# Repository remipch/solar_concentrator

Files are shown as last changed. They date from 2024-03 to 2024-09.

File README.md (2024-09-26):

# Solar Concentrator :sunny:

This project is a homemade automated solar concentrator :wrench: :sunny: :mag_right:

- [Overview](#overview)
- [Caution](#caution)
- [Key points](#key-points)
- [Technical breakdown](#technical-breakdown)
- [Next step](#next-step)
- [Licenses](#licenses)

## Overview

It consists of:
* An orientable mirror panel (currently 48 focusing mirrors, totaling 1m²)
* A fixed target (currently a simple concrete oven with a black metal plate and a tempered glass)
* The supervisor: an electronic control device that measures the target, computes and sends commands to the motors

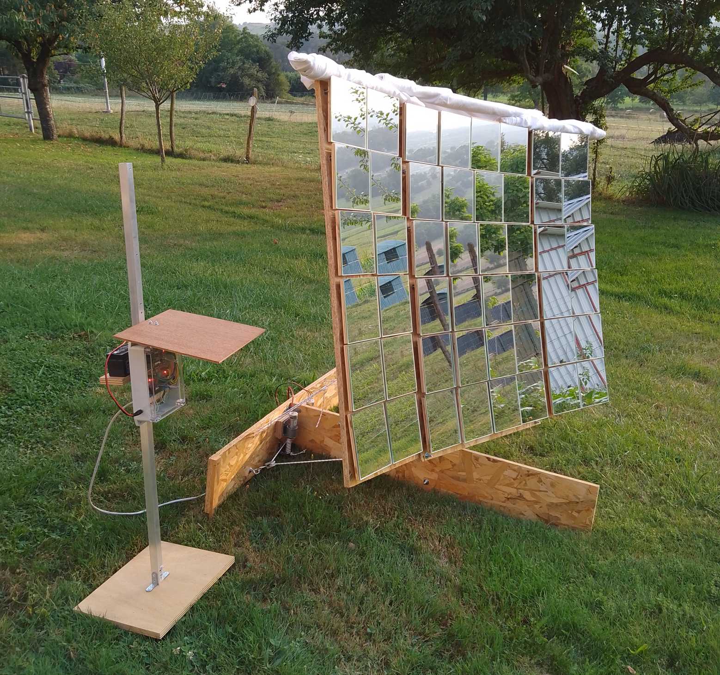
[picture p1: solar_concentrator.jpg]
Solar Concentrator


On 26 june 2024, when adding some aluminium foil inside the oven to improve insulation,
the oven temperature has risen to __210°C after 30 minutes__.

The video below shows the concentrator in action on 8 July 2024:
* First half of the video is the assembly (speed x10)
* Second half is the automatic sun tracking for about 7 hours (speed x600)

https://github.com/user-attachments/assets/06e3a9e1-d853-4ddd-b5d8-55cf9d6ecc89

## Caution

> [!CAUTION]
> :warning::warning: __THIS PROJECT MAY HARM PEOPLE OR ANIMALS IN THE SURROUNDINGS__ :warning::warning:
>
> It can __cause permanent blindness, burn skin or ignite objects__.
>
> Even when the concentrator is not powered, the sun remains concentrated 48 times in a single small area.
>
> This focal point is constantly __moving along a path that is difficult to predict__.
>
> In its current state, it __must be continuously monitored__ and the mirrors must be covered quickly in the event of an anomaly.

## Key points

* Can produce up to about __1000 watts of heat__ while __consuming 3.8 watts__ of electrical power :moneybag:
* Uses only standard, cheap and available components and materials :bricks: :nut_and_bolt:
* Does not require a high precision construction, everything can be built by hand with common tools :straight_ruler: :carpentry_saw:
* Easy to assemble and disassemble :screwdriver:
* Easy to understand and modify :mag_right:
* Open source :unlock:

Limitations of this version:
* There is no safety layer implemented (see warning above :warning:)
* An initial manual step is required to orient the panel before it can automatically track the sun
* Only one panel can be controlled
* Does not work on cloudy days (it is the user's responsibility to remove the clouds from the sky :smile:)
* Power consumption could be significantly reduced through the implementation of various low-power modes

To build this project, some products were happily "hacked" out of their original use:
* The tempered glass used in the oven is from an [Ikea shelf](https://www.ikea.com/fr/fr/p/komplement-tablette-en-verre-blanc-80257647/)
* The mirrors are [decorative bathroom mirrors](https://www.bricoman.fr/lot-6-miroirs-adhesif-carre-15x15-cm-1429043.html)
* The motors are cheap [model engines](https://www.gotronic.fr/art-motoreducteur-mfa-950d8101ln-11376.htm)

## Technical breakdown

The project structure reflects the technical breakdown.

Detailed information can be found in the corresponding subfolders:

* [Mechanics :gear:](mechanics/README.md) : 3D models of the parts used in the solar panel
* [Electronics :electric_plug:](electronics/README.md) : schematics and layout of the custom supervisor board
* Software :floppy_disk: :
    * [Simulator](software/simulator/README.md) : evaluates the theoretical power received by the target for a given hardware configuration
    * Supervisor controller : ESP32-CAM firmware based on [Espressif ESP32 framework](https://docs.espressif.com/projects/esp-idf/en/latest/esp32/index.html)
        * [Supervisor component](software/supervisor_controller/components/supervisor/README.md) defines the supervisor high level logic
        * [Sun tracker](software/supervisor_controller/components/sun_tracker/README.md) computes motors commands to keep the sun light at the center of the target area
        * [Target detector](software/supervisor_controller/components/target_detector/README.md) detects the target position in image
        * [Web interface](software/supervisor_controller/components/web_interface/README.md) allows the user to interact with the supervisor
        * [Motors component](software/supervisor_controller/components/motors/README.md) controls the motors from the ESP32 application
        * [Image component](software/supervisor_controller/components/image/README.md) provides general image processing functions
    * [Motors controller](software/motors_controller/README.md) : Arduino Pro Mini firmware for controlling motors

## Next step

The next step is to control any number of panels to obtain a power output of several kilowatts.

This would open up the following possibilities:
* Quickly boil a large volume of liquid
* Desalinate or sterilize a large volume of water
* Cook or sterilize a large volume of food
* Melt plastic, metal or glass
* Increase the output of photovoltaic panels with [concentrated photovoltaics](https://en.wikipedia.org/wiki/Concentrator_photovoltaics)

## Licenses

Copyright (C) 2024 Rémi Peuchot (https://remipch.github.io/)

* The software is distributed under [GNU GPL v3](LICENSE.md)
* Hardware designs (electronics and mechanics) are distributed under [CERN Open Hardware Licence v2 Strongly Reciprocal](LICENSE-HW.txt)

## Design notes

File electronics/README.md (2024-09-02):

# Solar Concentrator Electronics :electric_plug:

This folder contains the custom electronics designed for the supervisor.

- [Overview](#overview)
- [Supervisor Board](#supervisor-board)
    - [Schematics](#schematics)
    - [Components](#components)
    - [Top layer](#top-layer)
    - [Bottom layer](#bottom-layer)
    - [3D model](#3d-model)
    - [Photos](#photos)
    - [BOM](#bom)
- [Electronic case](#electronic-case)
    - [Photos](#photos)
    - [BOM](#bom)

## Overview

A custom board has been designed using [LibrePCB](https://librepcb.org) and produced by [AISLER](https://aisler.net).

It doesn't do anything complicated, just glues things together :
* Allows to connect the ESP32-CAM board
* Allows to connect the Arduino Pro Mini board
* Includes connectors for 2 mirror panels
* Includes a voltage regulator to convert the battery voltage from 12V to 5V
* Includes some switches to turn ON/OFF the child boards
* Includes a FTDI connector to upload the ESP32-CAM firmware in place (Arduino has its own FTDI connector)
* Includes a minimal voltage converter for the child boards to communicate with each other

Everything is assembled in an electronic case with a few external connectors for power and panels.

> [!NOTE]
> The electronics can control two panels but the current software only controls one.

Electronics overview

## Supervisor Board

### Schematics

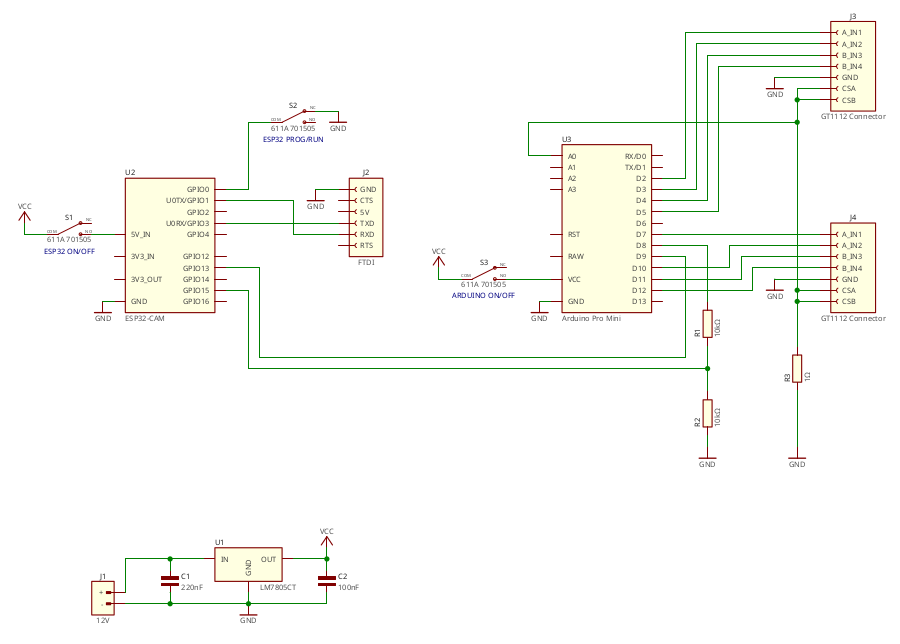
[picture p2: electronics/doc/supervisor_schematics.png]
Supervisor board schematics


### Components

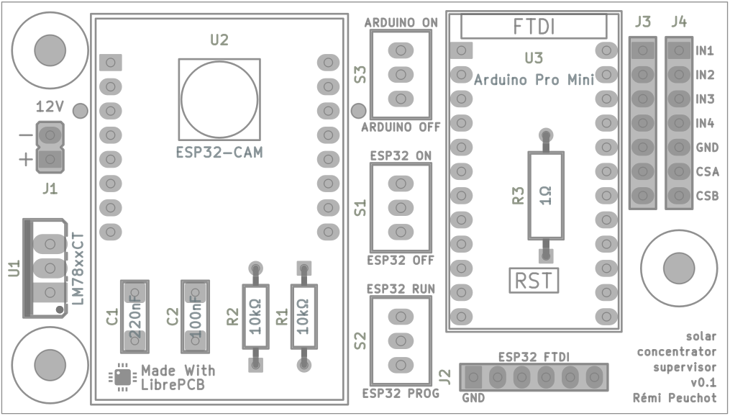
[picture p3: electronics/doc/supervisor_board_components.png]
Supervisor board components


### Top layer

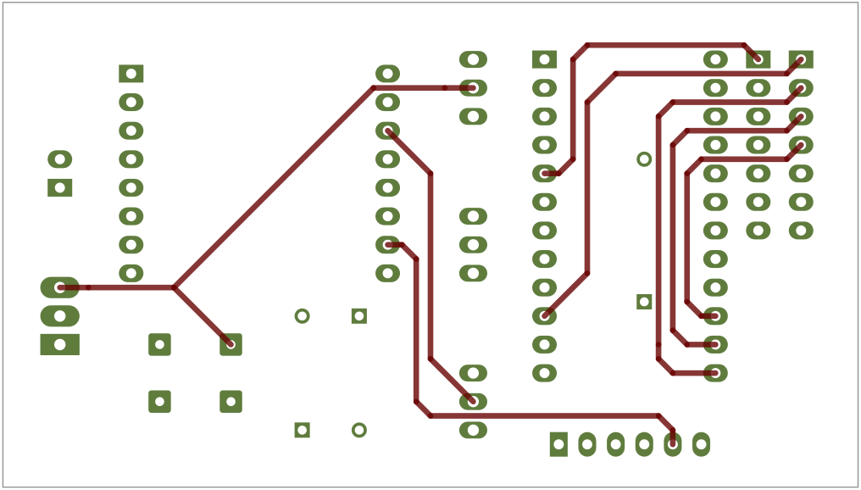
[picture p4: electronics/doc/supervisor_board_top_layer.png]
Supervisor board top layer


(ground plane is not shown)

### Bottom layer

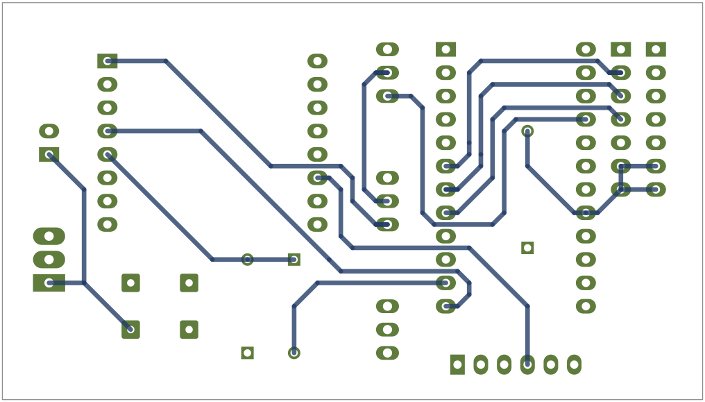
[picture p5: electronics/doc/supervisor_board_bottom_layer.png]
Supervisor board bottom layer


(ground plane is not shown)

### 3D model

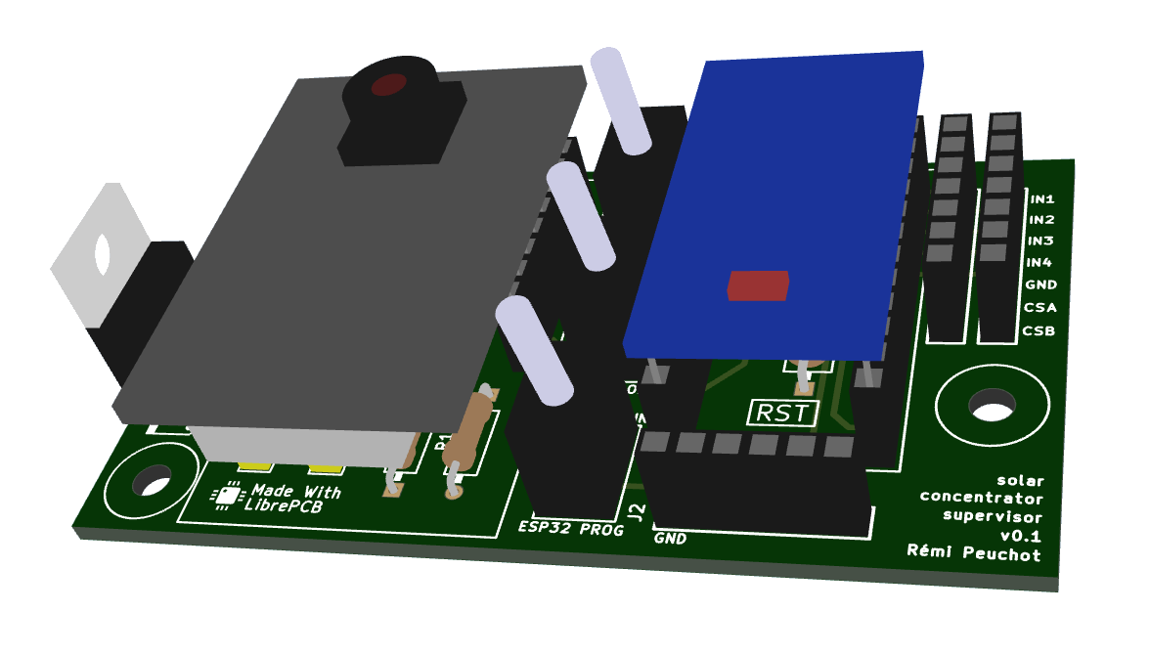
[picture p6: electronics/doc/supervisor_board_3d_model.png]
Supervisor board 3d


### Photos

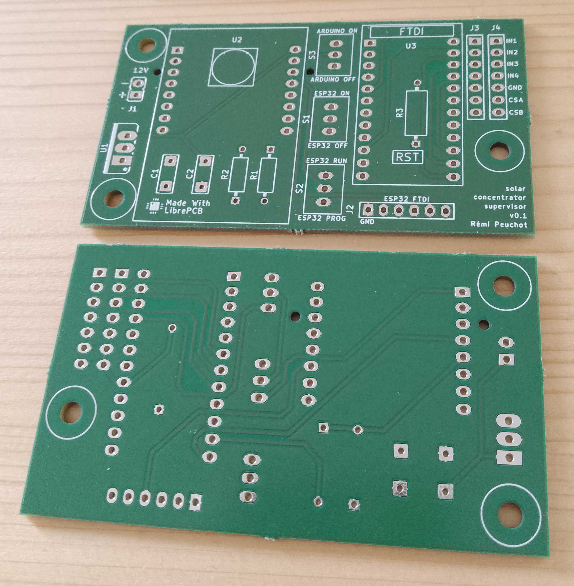
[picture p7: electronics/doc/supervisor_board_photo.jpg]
Supervisor empty board


### BOM

| Count | Unit Price (€) | Description
| ----- | --- | ---
| 1 | 14.3 | [ESP32-CAM](https://www.gotronic.fr/art-module-esp32-cam-32630.htm)
| 1 | 8.95 | [Arduino Pro Mini](https://www.gotronic.fr/art-carte-dfrduino-pro-mini-dfr0159-19247.htm)
| 2 | 0.6 | [Female socket FH1X6](https://www.gotronic.fr/art-connecteur-fh1x6-22732.htm)
| 2 | 0.65 | [Female socket FH1X7](https://www.gotronic.fr/art-connecteur-fh1x7-22733.htm)
| 2 | 0.75 | [Female socket FH1X8](https://www.gotronic.fr/art-connnecteur-fh1x8-22734.htm)
| 2 | 1.0 | [Female socket FH1X12](https://www.gotronic.fr/art-connecteur-fh1x12-24494.htm)
| 1 | 0.6 | [Male socket HE14](https://www.gotronic.fr/art-connecteur-he14-mh100-4457.htm)
| 1 | 0.5 | [Voltage regulator LM7805](https://www.gotronic.fr/art-l7805cv-1578.htm)
| 1 | 0.2 | [Capacitor 220 nF](https://www.gotronic.fr/art-condensateur-lcc-220-nf-3271.htm)
| 1 | 0.2 | [Capacitor 100 nF](https://www.gotronic.fr/art-condensateur-lcc-100-nf-66.htm)
| 1 | 0.1 | [Resistor 1 ohm 1 W](https://www.gotronic.fr/art-resistance-carbone-1w-1-0-8486-2713.htm)
| 1 | 0.2 | [10 Resistor 10 kohm 0.25 W](https://www.gotronic.fr/art-10-resistances-1-4w-10k-8486-19.htm)
| 3 | 3.3 | [Small switch](https://www.conrad.fr/fr/p/interrupteur-a-levier-250-v-ac-0-15-a-1-x-on-on-611a-permanent-1-pcs-1566114.html)

## Electronic case

### Photos

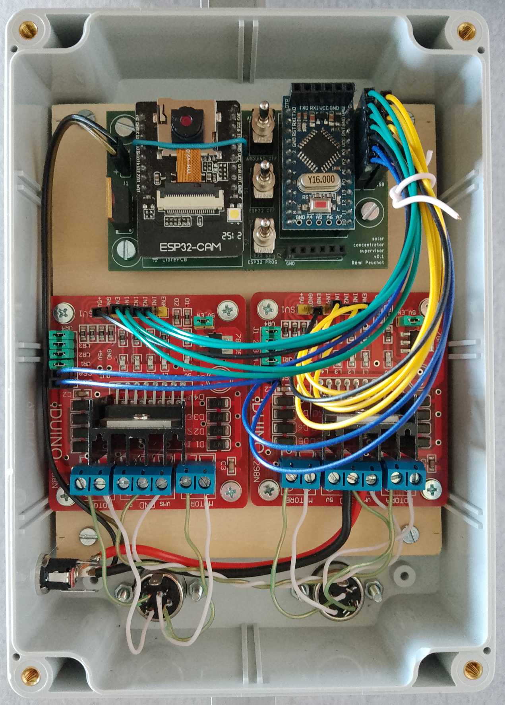
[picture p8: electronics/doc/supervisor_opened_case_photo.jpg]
Supervisor opened case


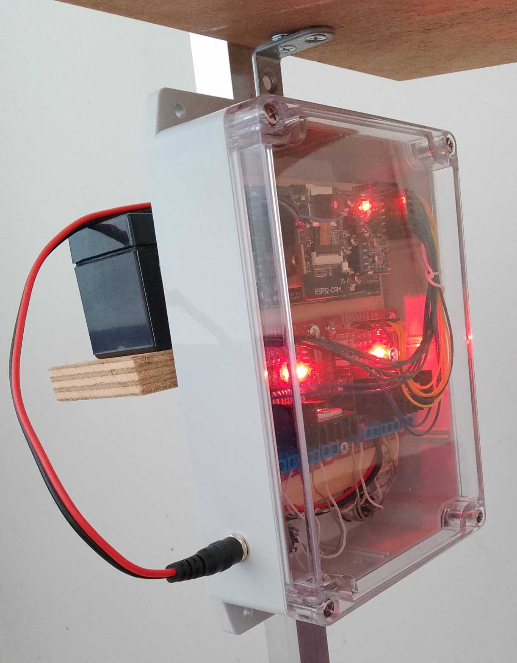
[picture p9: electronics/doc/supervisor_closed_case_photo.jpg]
Supervisor closed case


### BOM

| Count | Unit Price (€) | Description
| ----- | --- | ---
| 1 | 16.9 | [ABS case](https://www.gotronic.fr/art-boitier-abs-etanche-g214cmf-33575.htm)
| 3 | 1.5 | [10 cable M/F](https://www.gotronic.fr/art-pack-de-10-cables-de-connexion-m-f-bbj21-27098.htm)
| 1 | 1.9 | [Female power socket](https://www.gotronic.fr/art-embase-alim-sc215-123.htm)
| 1 | 1.5 | [Male power cable](https://www.gotronic.fr/art-2-cordons-d-alim-5-5-x-2-1-mm-male-22394.htm)
| 2 | 1.2 | [Female DIN socket PB560](https://www.gotronic.fr/art-embase-pb560-4764.htm)
| 2 | 1.0 | [Male DIN plug FM560](https://www.gotronic.fr/art-fiche-din-fm560-4748.htm)
| 2 | 6.5 | [Motor Driver GT1112](https://www.gotronic.fr/art-commande-de-2-moteurs-gt1112-26137.htm)
| 1 | 3.0 | A handful of M3 bolts, nuts, washers and spacers

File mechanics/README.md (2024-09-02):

# Solar Concentrator Mechanics :gear:

This folder contains the 3D models of the parts used in the solar panel.

- [Overview](#overview)
- [Solar panel](#solar-panel)
    - [Stand](#stand)
        - [Stand back board](#stand-back-board)
            - [Motor block](#motor-block)
        - [Stand front board](#stand-front-board)
    - [Panel frame](#panel-frame)
        - [Panel horizontal axis](#panel-horizontal-axis)
        - [Panel vertical axis](#panel-vertical-axis)
    - [Panel board](#panel-board)

## Overview

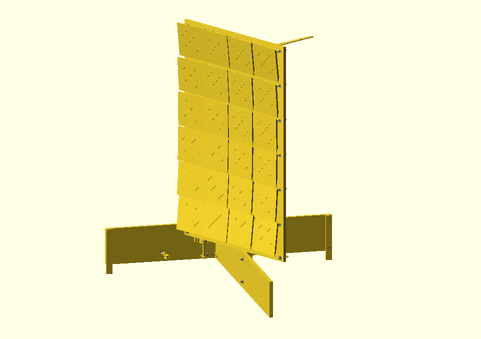
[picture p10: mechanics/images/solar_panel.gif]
Solar panel animation


The originality of the mechanical design is to use a simple [cablebot](https://en.wikipedia.org/wiki/Cable_robots) instead
of a traditional 2 axis tracker where each axis has a its own motor.
* Advantage: cheaper motors and cheaper mechanical structure can be used.
* Drawback: each axis cannot be controlled independently.

Another originality is the way in which each mirror orientation
can be precisely adjusted without the need for high-precision mechanics.

The mechanical parts have been modeled with [OpenSCAD](https://openscad.org/).

The documented model contains a single panel board with 24 mirrors.
Two 'wings' have been added to the sides to add 24 mirrors but are not documented here
(see the photo and video in the top-level README).

> [!TIP]
> __You can click on the images below to view them in an online 3D viewer.__

## Solar panel

> [!NOTE]
> The cable is not modeled because I couldn't find an easy way to do it with OpenSCAD.
>
> Each cable is actually wrapped around the motor axis, then passed through the pulley
> and tied to a fixed ring in the corner of the panel
> (see the photo and video in the top-level README).

| Assembled | Exploded |
| --- | --- |
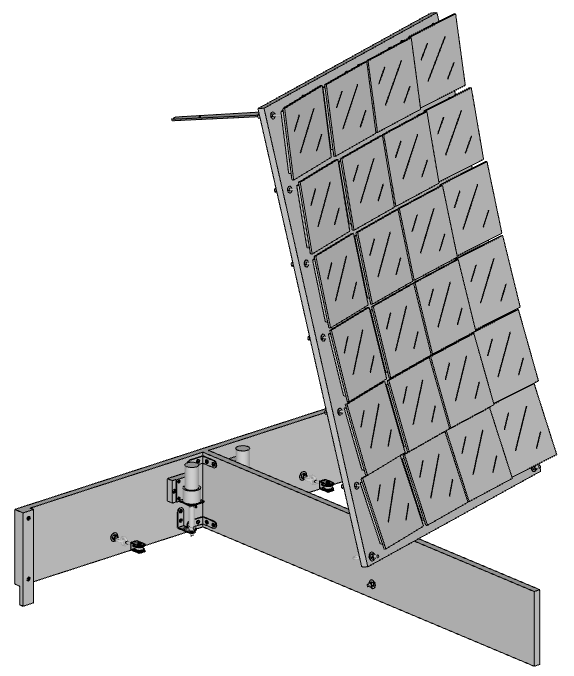
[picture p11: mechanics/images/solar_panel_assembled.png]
Solar panel
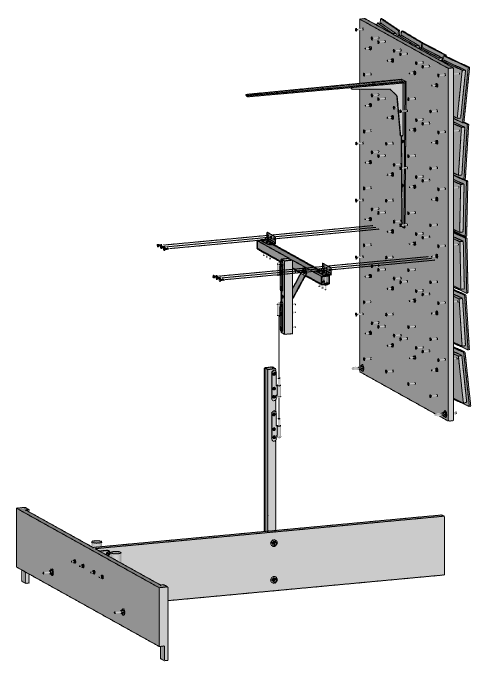
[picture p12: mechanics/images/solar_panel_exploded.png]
Solar panel
|  | 

A 'solar panel' consists of the following parts:

| Count | Description |
| ----- | --- |
| 1 | [Stand](#stand)
| 1 | [Panel frame](#panel-frame)
| 1 | [Panel board](#panel-board)
| 6 | Wood screw D4mm L15mm
| 2 | Cable (not shown in model)
| 1 | Counterweight 3kg (not shown in model)

### Stand

| Assembled | Exploded |
| --- | --- |
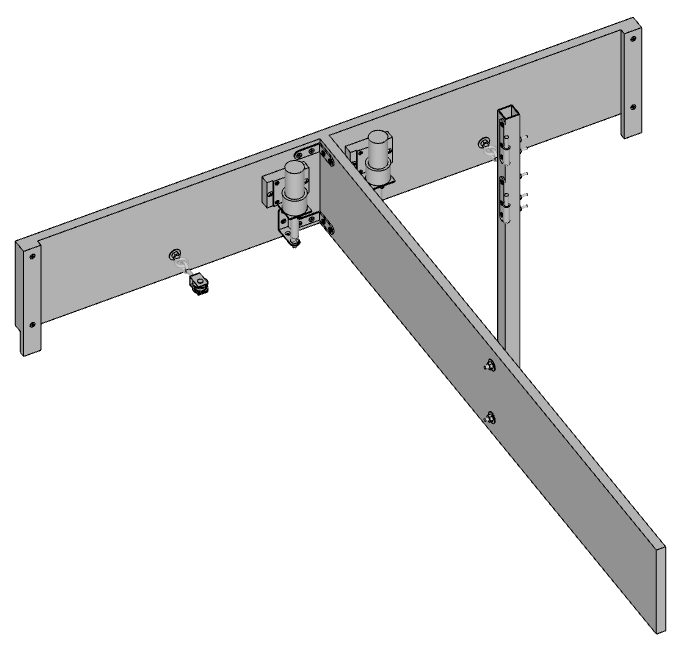
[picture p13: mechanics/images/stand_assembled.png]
Stand
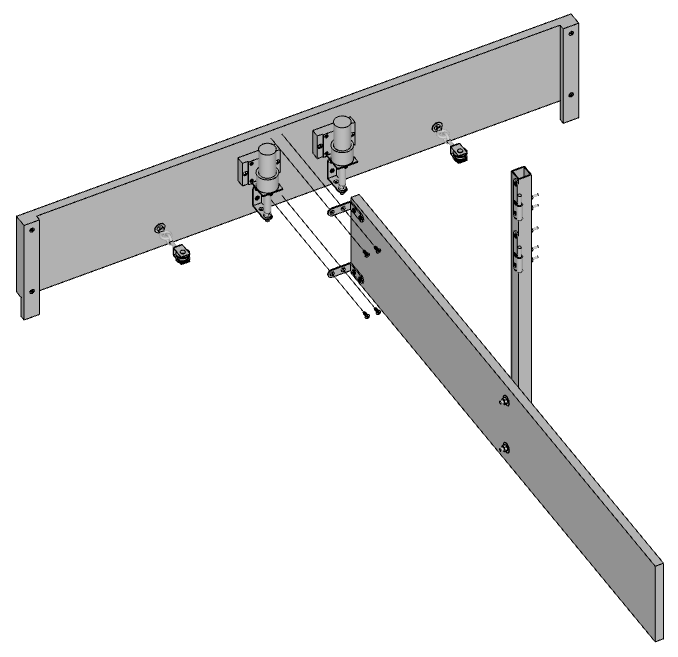
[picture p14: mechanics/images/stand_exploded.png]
Stand
|  | 

A 'stand' consists of the following parts:

| Count | Description |
| ----- | --- |
| 1 | [Stand back board](#stand-back-board)
| 1 | [Stand front board](#stand-front-board)
| 4 | Wood screw D4mm L15mm

#### Stand back board

| Assembled | Exploded |
| --- | --- |
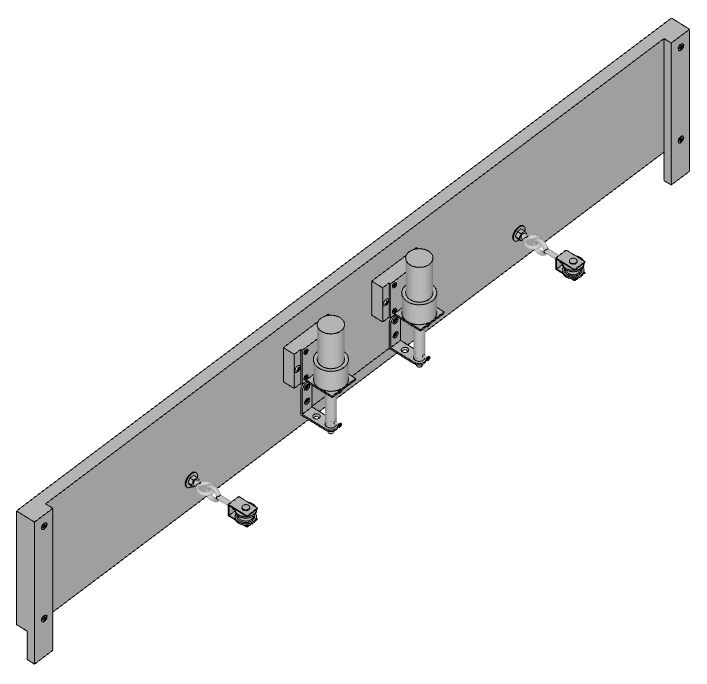
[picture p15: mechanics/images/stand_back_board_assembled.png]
Stand back board
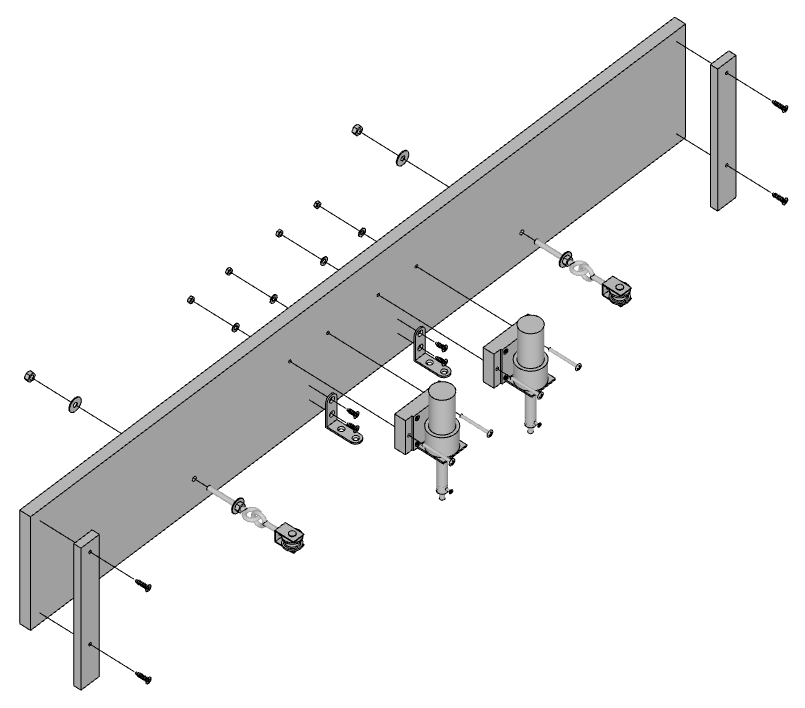
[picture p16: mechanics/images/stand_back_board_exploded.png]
Stand back board
|  | 

A 'stand back board' consists of the following parts:

| Count | Description |
| ----- | --- |
| 2 | [Motor block](#motor-block)
| 1 | Wood board W1000mm D15mm H160mm
| 2 | Wood leg W28mm D10mm H200mm
| 2 | [Pulley](https://www.leroymerlin.fr/produits/quincaillerie/corde-sangle-sandow-chaine-cable/accessoires-de-corde-de-cable-de-chaine/poulie-a-piton-acier-zingue-standers-diam-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) with washer and nut
| 2 | Small bracket
| 4 | Wood screw D4mm L15mm
| 4 | Wood screw D4mm L20mm
| 4 | Round head bolt M4 L40mm with washer and nut

##### Motor block

| Assembled | Exploded |
| --- | --- |
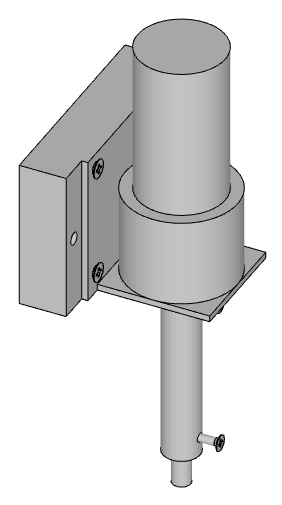
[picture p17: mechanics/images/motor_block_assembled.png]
Motor block
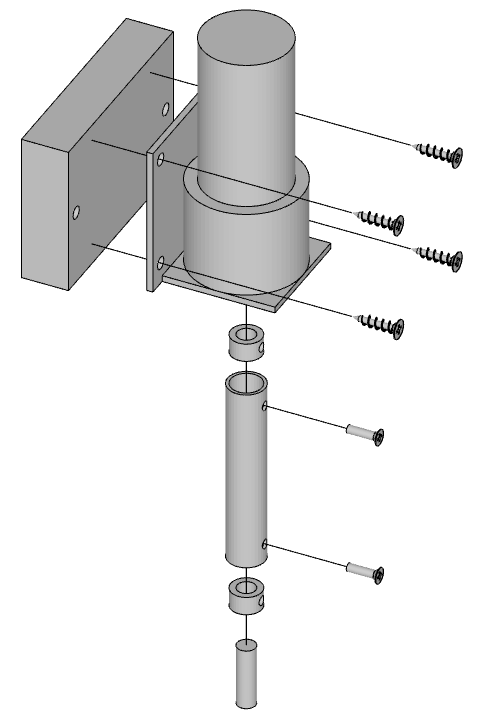
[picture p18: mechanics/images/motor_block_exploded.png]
Motor block
|  | 

A 'motor block' consists of the following parts:

| Count | Description |
| ----- | --- |
| 1 | [Model engine](https://www.gotronic.fr/art-motoreducteur-mfa-950d8101ln-11376.htm)
| 1 | [Engine bracket](https://www.gotronic.fr/art-support-pour-motoreducteurs-mfa-727-22944.htm)
| 1 | Wood board W68mm D15mm H48mm
| 2 | [Locking ring](https://www.conrad.fr/fr/p/bagues-d-arret-modelcraft-10347-6-mm-225436.html) d6mm D10mm L5mm
| 2 | Countersunk bolt M3 L14mm
| 1 | Cylindrical steel tube L60mm d10mm D12mm
| 1 | Cylindrical steel rod L20mm D6mm
| 4 | Wood screw D3mm L15mm

#### Stand front board

| Assembled | Exploded |
| --- | --- |
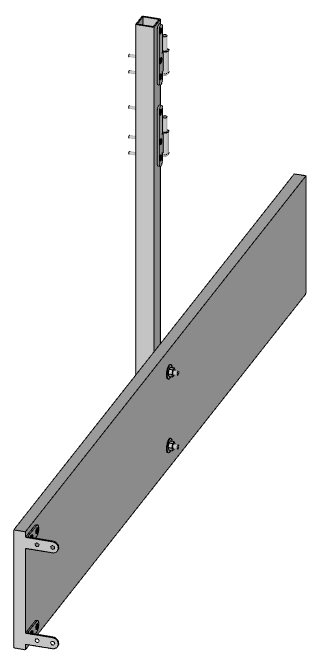
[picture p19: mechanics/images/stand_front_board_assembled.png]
Stand front board
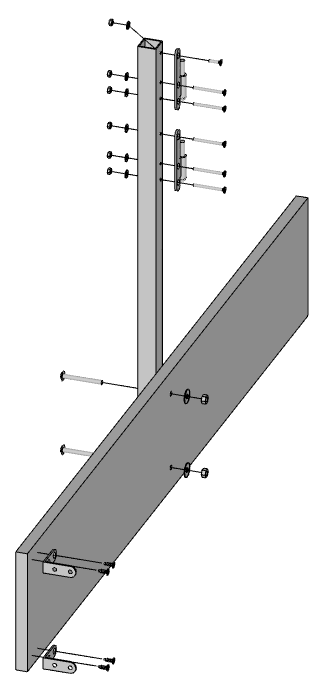
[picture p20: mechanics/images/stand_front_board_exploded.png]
Stand front board
|  | 

A 'stand front board' consists of the following parts:

| Count | Description |
| ----- | --- |
| 2 | [Left hinge](https://www.bricomarche.com/p/paumelle-bois-bout-rond-80x40mm-gauche-zingue/3479045300500) male
| 1 | Aluminium square tube W23.5mm L600mm
| 2 | Small bracket
| 1 | Countersunk bolt M4 L15mm with washer and nut
| 5 | Countersunk bolt M4 L40mm with washer and nut
| 2 | Round head bolt M6 L50mm with washer and nut
| 4 | Wood screw D4mm L15mm

### Panel frame

| Assembled | Exploded |
| --- | --- |
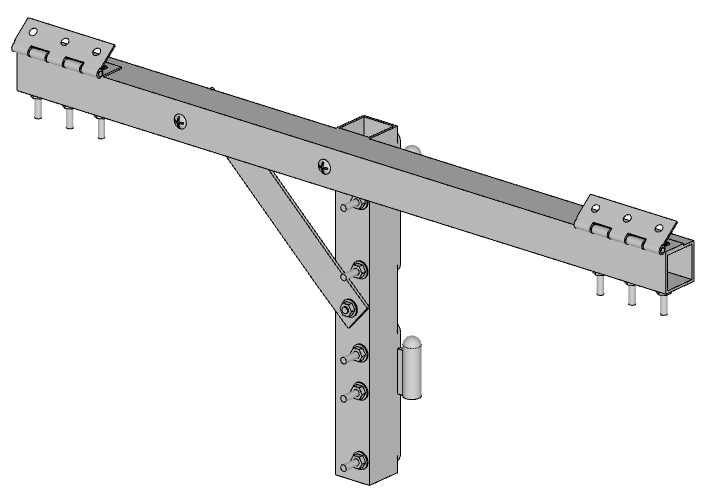
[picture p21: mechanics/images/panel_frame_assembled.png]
Panel frame
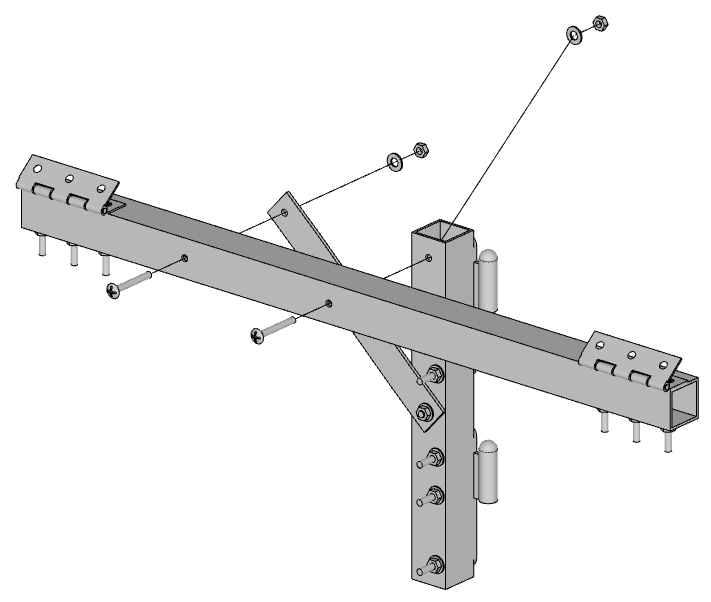
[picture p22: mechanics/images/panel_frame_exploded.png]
Panel frame
|  | 

A 'panel frame' consists of the following parts:

| Count | Description |
| ----- | --- |
| 1 | [Panel horizontal axis](#panel-horizontal-axis)
| 1 | [Panel vertical axis](#panel-vertical-axis)
| 2 | Round head bolt M4 L30mm with washer and nut

#### Panel horizontal axis

| Assembled | Exploded |
| --- | --- |
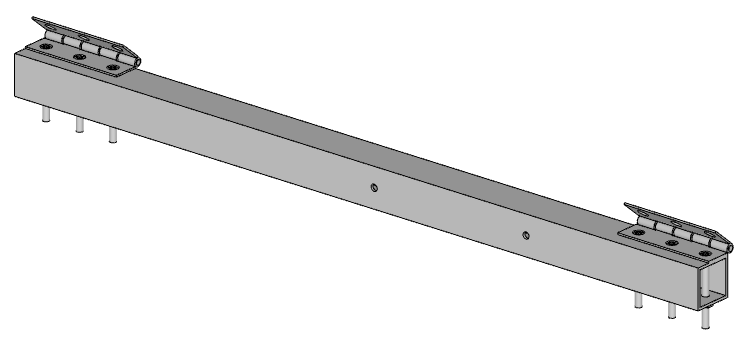
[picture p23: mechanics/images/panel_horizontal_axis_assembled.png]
Panel horizontal axis
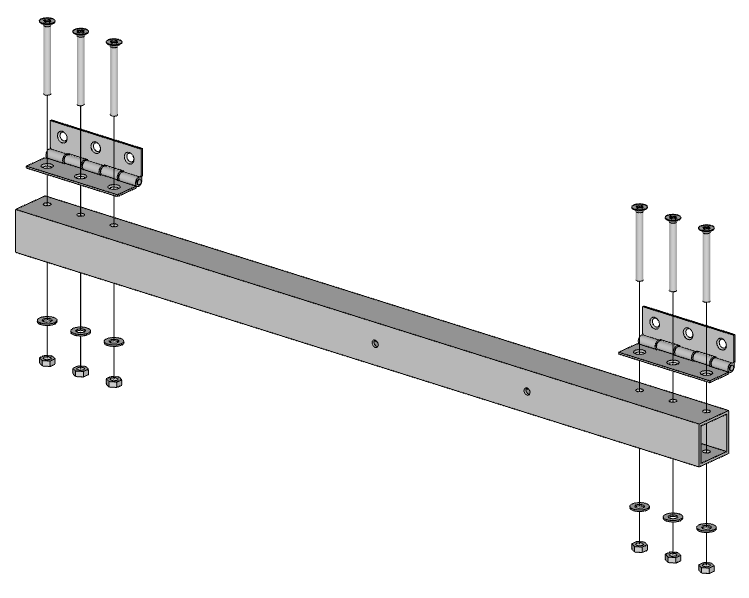
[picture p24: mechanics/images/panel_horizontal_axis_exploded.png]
Panel horizontal axis
|  | 

A 'panel horizontal axis' consists of the following parts:

| Count | Description |
| ----- | --- |
| 1 | Aluminium square tube W23.5mm L450mm
| 6 | Countersunk bolt M4 L40mm with washer and nut
| 2 | Small hinge

#### Panel vertical axis

| Assembled | Exploded |
| --- | --- |
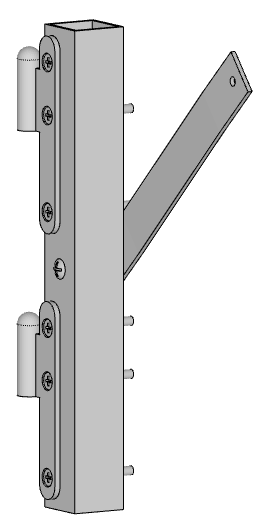
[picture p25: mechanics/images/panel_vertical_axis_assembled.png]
Panel vertical axis
|  | Panel vertical axis

A 'panel vertical axis' consists of the following parts:

| Count | Description |
| ----- | --- |
| 2 | [Left hinge](https://www.bricomarche.com/p/paumelle-bois-bout-rond-80x40mm-gauche-zingue/3479045300500) female
| 1 | Aluminium square tube W23.5mm L200mm
| 1 | Aluminium flat profile W20mm D2mm
| 1 | Countersunk bolt M4 L15mm with washer and nut
| 5 | Countersunk bolt M4 L40mm with washer and nut
| 2 | Round head bolt M4 L30mm with washer and nut

### Panel board

| Assembled | Exploded |
| --- | --- |
| Panel board | Panel board

A 'panel board' consists of the following parts:

| Count | Description |
| ----- | --- |
| 1 | Wood board W620mm D15mm H960mm
| 24 | Wood part W130mm D10mm H130mm
| 1 | [Big bracket](https://www.leroymerlin.fr/produits/rangement-dressing/etagere/fixation-etagere/equerre-etagere/equerre-normo-acier-peint-blanc-h-45-x-p-40-cm-85002102.html)
| 24 | [Mirror](https://www.bricoman.fr/lot-6-miroirs-adhesif-carre-15x15-cm-1429043.html)
| 1 | [Mirror glue](https://www.leroymerlin.fr/produits/decoration-eclairage/dalle-rosace-et-moulure/colle-dalle-rosace-et-moulure/colle-de-fixation-ms-polymere-verre-et-miroir-pattex-3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)
| 72 | [Impact nut](https://www.vis-express.fr/ecrou-a-griffes/31277-1004768-ecrou-a-griffes-m4-acier-zing-blanc-3663072090095.html)
| 96 | Countersunk bolt M4 L60mm
| 24 | M4 washer and nut
| 2 | Fixed ring with washer and nut
| 3 | Wood screw D4mm L15mm

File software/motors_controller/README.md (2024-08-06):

# motors controller

'motors_controller' manages the following features in a separate arduino Pro Mini board :
- analog input to measure motors current
- digital output to command motor drivers

Because it's not possible to manage everything simultaneously on ESP32-CAM board :
- wifi + analog input
- serial + digital pins (6 pins required to command motors)

The main supervisor_controller board (ESP32-CAM) communicates with this motors_controller
via I2C with a simple specific protocol consisting of sending a simple string with text commands.

## Commands syntax

Several commands can be sent together : `<command1>;<command2>;<command3>`

They will be buffered on arduino side and executed sequentially after the 'run' command is received.

All commands are in the same form : `<command_id>:<arg1>[,<arg2[,<arg3>]]`

* Stop and clear command : `c`

* Print state immediately : `s`

* Print all buffered commands immediately : `p`

* Print measure buffer immediately `m:<samples_count>`

* Set measure sampling : `ms:<period_ms>,<samples_count>`

* Set output level : `l:<output_level>` with :
    - `output_level` (between 0 and 255): value written to PWM_PIN to allow output voltage customization.

* Set motors output : `o:<motor_pins>,<max_time_ms>,<threshold>` with :
    - `motors_pin`: the integer value of all output pins
    - `max_time_ms`: max time before stopping motors
    - `threshold`: measured current threshold (0 to 1023) where motor must be stopped

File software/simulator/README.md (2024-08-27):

# Solar Concentrator Simulator

Before any hardware construction, a simulator was developed
using [Panda3D](https://www.panda3d.org/), a Python game engine.

This simulator can simulate between 1 and 10 panels of different sizes,
immersed in an environment including some background elements.

Its simple user interface allows to configure:
* the global position on the planet
* the date and time
* the size and position of the background elements
* the number, size and position of the panels in the grid

From such a given configuration, it simulates the reflection of solar rays
(taking into account the shadows) and estimates the corresponding power received on the target area.

> [!NOTE]
> This simulator has been developed iteratively, its source code is not very clean,
> its user interface can be slow and laggy.

From the provided docker container, the simulator can be started with the following command:

``` bash
cd /solar_concentrator/software/simulator/sources

python3 solar_concentrator_simulator.py
```

A remote control allows to send configuration values and get estimated output values
from an external Python program. Any parameter that can be set manually can also
be set remotely with this `remote_control`.

This is used for two purposes :
* `end_to_end_test.py` starts the simulator, sets some configuration values and checks
if the estimated power value is as expected
* `time_walker_recorder.py` uses the current simulator configuration and estimates
the received solar power for a given time range

The following animation is a screenshot of the solar concentrator:

Solar concentrator screenshot

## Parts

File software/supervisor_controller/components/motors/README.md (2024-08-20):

# Motors component

This component allows to control the motors from the ESP32 application.

It sends commands to the external motors_controller board via serial pins, read the reply
and manages the current motors state.

It's split into a few files :

Motors diagram

`motors` is the public interface of the motors component.

It wraps `motors_state_machine` under esp32 specific tools
(task, thread safety, event, signals, etc.).

It shoud not implement any logic by itself.

`motors_state_machine` is the core logic implementation of the component.

Splitting `motors_state_machine` from esp32 ecosystem allows to test
the core logic of this component :
- independently from esp32 ecosystem
- in simple, reproducible, single-threaded unit tests
- executed on host for rapid validation and feedback

`motors_state_machine` is not thread-safe by itself, its function must
never been called simultaneously.

`motors_hw` contains the minimal code to wrap
`motors_state_machine` "high level" decisions to specific hardware details.
It internally defines the gpio pins to use and the various hardware configs.

`motors_direction` declares public data structures of the motors component.

The following diagram is a slightly simplified representation of `motors_state_machine` :

State machine

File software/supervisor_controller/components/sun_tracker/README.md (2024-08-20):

# Sun tracker component

The `sun_tracker` component goal is to keep the sun light at the center of the target area.

Its main steps are :
- use camera to capture image
- use target_detector to detect the target area (where the spot light must be kept)
- use its own logic to detect the spot light and
deduce the eventual move direction to get closer to the target area center
- use motors to start move in the previously deduced direction
- listen motors to know when the move is finished

Its implementation is split in 3 layers :
- `sun_tracker` is the public interface of the component. It hides the internal synchronisation details
(mutex, tasks, etc.) and provide a minimal set of functions to use the component.
It does not implement logic by itself but provides thread safety to `sun_tracker_state_machine` layer.
- `sun_tracker_state_machine` manages the current state and react to external or internal transitions.
- `sun_tracker_logic` implements the component logic itself.

This separation allows to develop and test the state_machine and logic independently from the specific
platform (thread, mutex, synchronisation, etc.). These tests can be launched from host (see tests_on_host subfolder).

The following diagram is a slightly simplified representation of `sun_tracker_state_machine` :

State machine

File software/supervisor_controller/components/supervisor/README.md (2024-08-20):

# Supervisor component

This component implements the high level logic of the ESP32 application.

The `web_interface` component calls its minimal set of functions to react to user actions.

The following diagram is a slightly simplified representation of its internal state machine :

State machine

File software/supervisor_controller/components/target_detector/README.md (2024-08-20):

# Target detector component

The goal of `target_detector` component is to detect the rectangle area that will be considered as the target to sun rays.

To accomplish this, it uses a modified version of QR-code detector (quirc) that detect corner capstones.

From the detected capstone positions in image, it applies a hard-coded geometric pattern to compute the rectangle area.

Each capstone is detected with a width and a height :

```
              w
            ◄───►
         ▲  ┌───┐
        h│  │   │
         ▼  └───┘
```

If 4 capstones are successfully detected, the following pattern is applied from capstones :

```
            ┌───┐               ┌───┐─ ─▲
        ▲─ ─│ 1 │               │ 2 │   │h
        │   └───┘               └───┘─ ─▼
     2*h│   │                       │
        │   │                       │
        ▼─ ─┌───────────────────────┐
            │                       │
            │        target         │
            │         area          │
            │       rectangle       │
            │                       │
       ─▲─ ─└───────────────────────┘
        │   │                       │
     2*h│   │                       │
        │   ┌───┐               ┌───┐
        ▼─ ─│ 3 │               │ 4 │
            └───┘               └───┘
```

Given that capstone positions are not strictly aligned vertically and horizontally in real images,
the area rectangle is adjusted to always fit in the rectangle shown above :

```
  left_border = max(corner_1.left, corner_3.left)
  right_border = min(corner_2.right, corner_4.right)
  top_border = max(corner_1.center_y, corner_2.center_y) + 2 * average_corner_height
  bottom_border = min(corner_3.center_y, corner_4.center_y) - 2 * average_corner_height
```

This simple approch is valid as long as the perspective effect is negligible in images :
- the real target surface is almost perpendicular to the camera optical axis
- target and camera are almost horizontal

Moreover, a few simple harcoded checks are applied :
- vertical and horizontal misalignments must be less than minimal capstone size
- rectangle size must be greater than maximal capstone size

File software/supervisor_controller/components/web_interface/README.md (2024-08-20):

# Web interface component

This component provides a minimal http server serving a single web page
to control the supervisor.

It has been started from esp32 `web_custom` example and iteratively changed
to bring supervisor features.

Note: the web page is designed for smartphone only
(it works on larger screen but it's not optimal).

Here is a screenshot of the resulting web page :

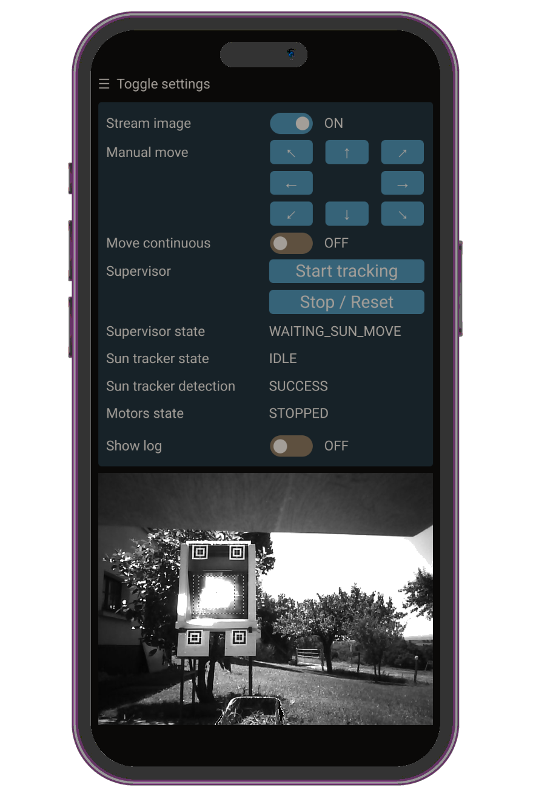
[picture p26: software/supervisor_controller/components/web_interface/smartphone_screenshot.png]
Smartphone mockup


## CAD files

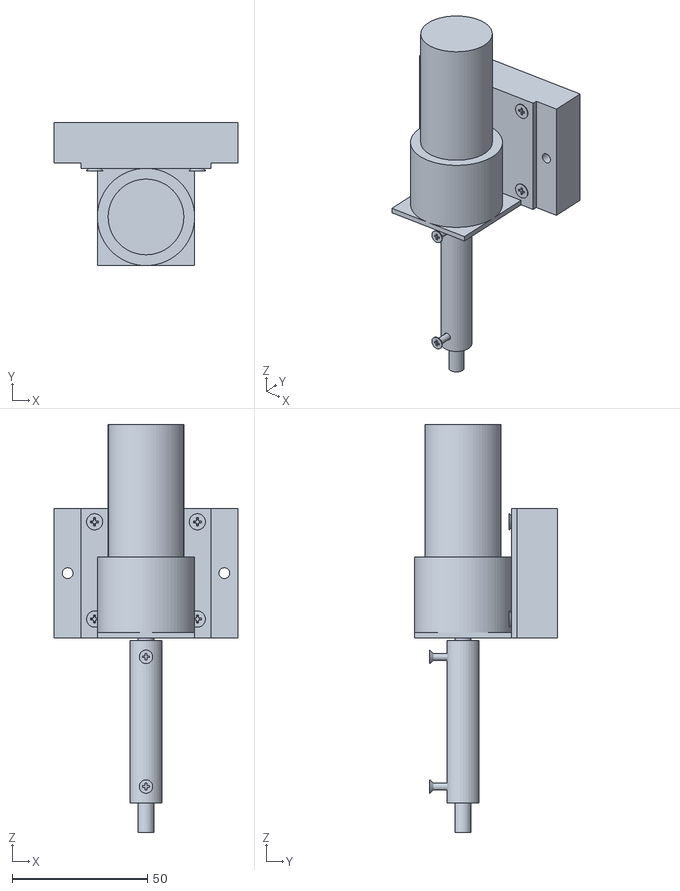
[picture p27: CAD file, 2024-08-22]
mechanics/web_viewer/models/motor_block_assembled.stl
68.0 x 53.0 x 151.0

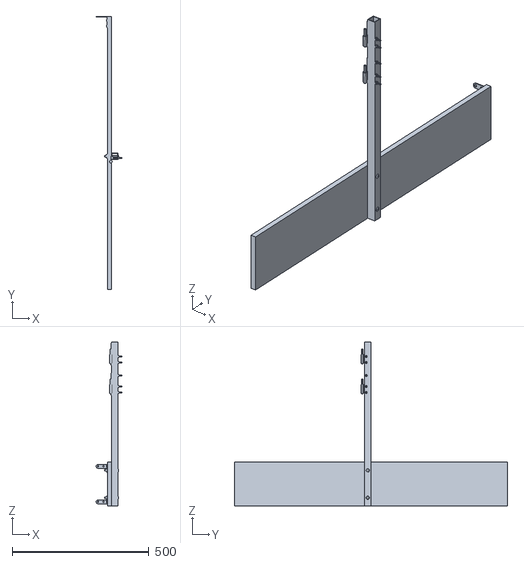
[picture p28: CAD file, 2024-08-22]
mechanics/web_viewer/models/stand_front_board_assembled.stl
95.0 x 1000.0 x 600.0

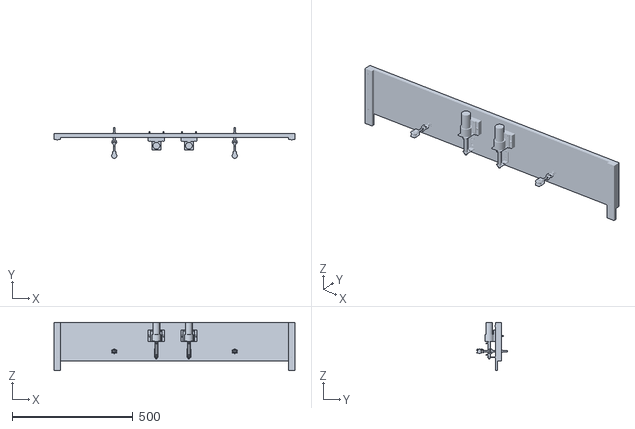
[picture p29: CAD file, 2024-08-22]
mechanics/web_viewer/models/stand_back_board_assembled.stl
1000.0 x 127.0 x 200.0

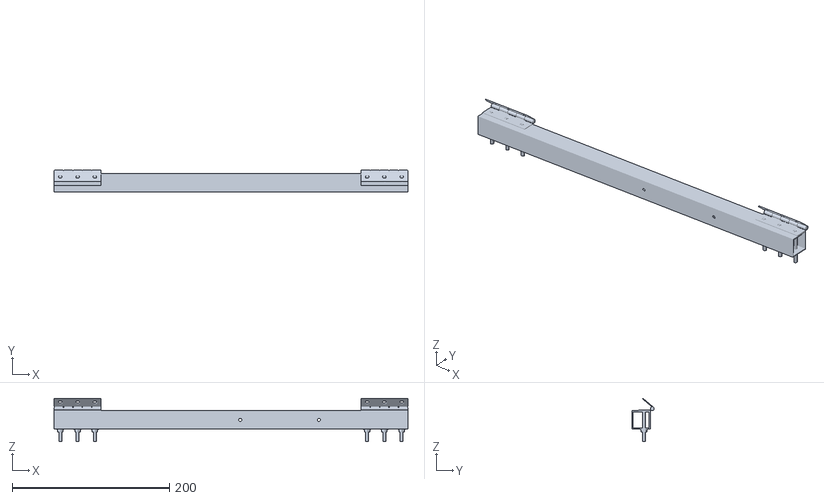
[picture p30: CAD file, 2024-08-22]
mechanics/web_viewer/models/panel_horizontal_axis_assembled.stl
450.0 x 28.5 x 55.2

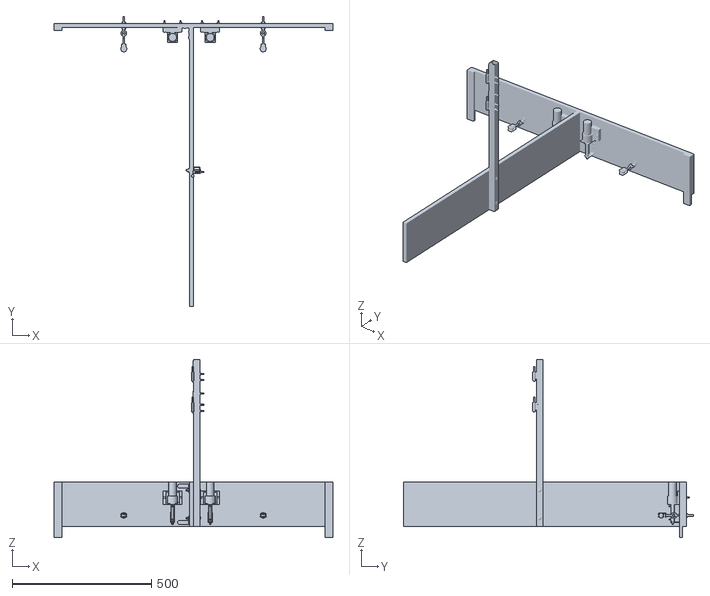
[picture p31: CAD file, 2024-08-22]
mechanics/web_viewer/models/stand_assembled.stl
1000.0 x 1040.0 x 640.0

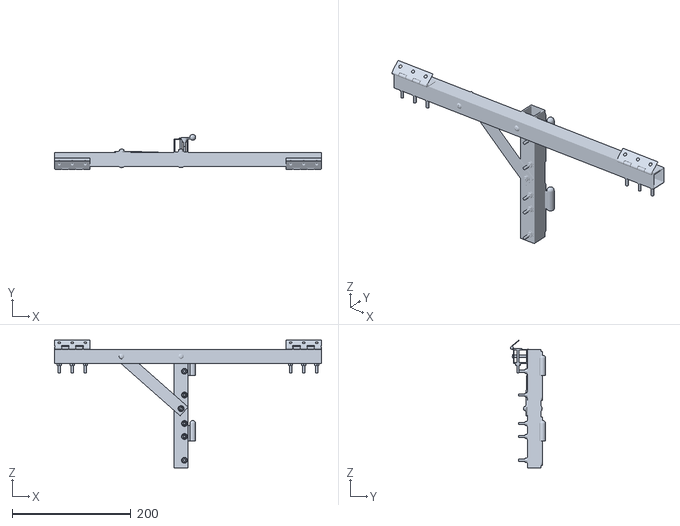
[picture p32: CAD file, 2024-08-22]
mechanics/web_viewer/models/panel_frame_assembled.stl
450.0 x 59.5 x 215.7

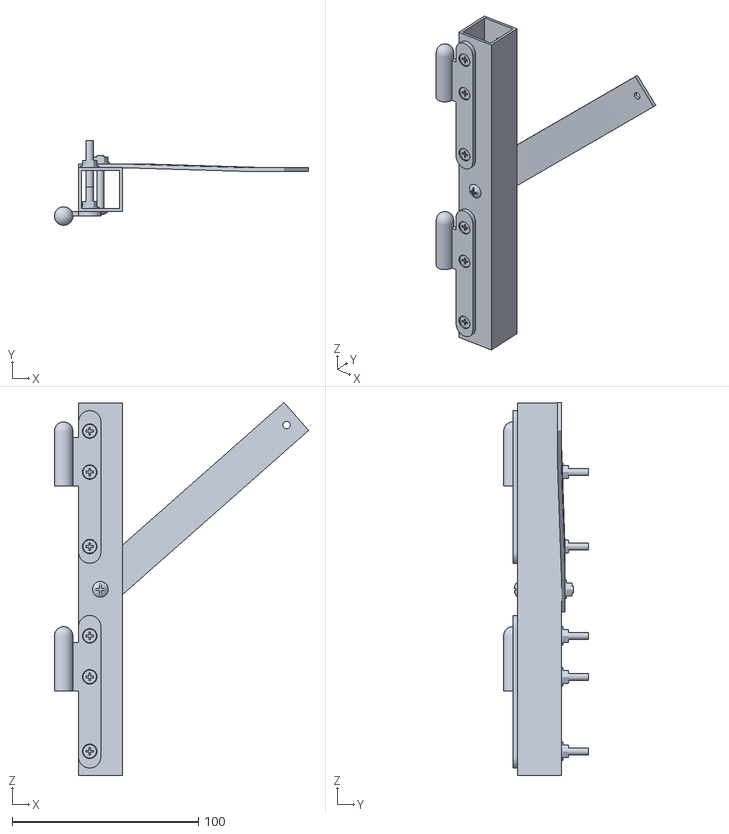
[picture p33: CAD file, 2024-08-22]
mechanics/web_viewer/models/panel_vertical_axis_assembled.stl
136.6 x 45.5 x 200.4

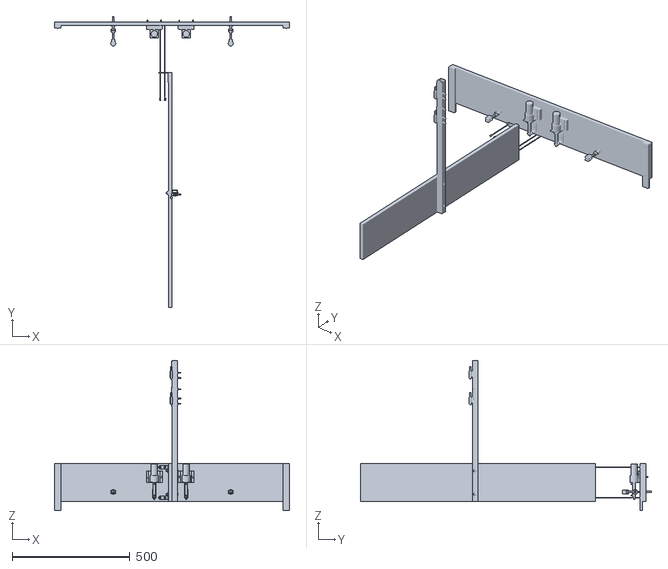
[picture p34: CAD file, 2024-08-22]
mechanics/web_viewer/models/stand_exploded.stl
1000.0 x 1240.0 x 640.0

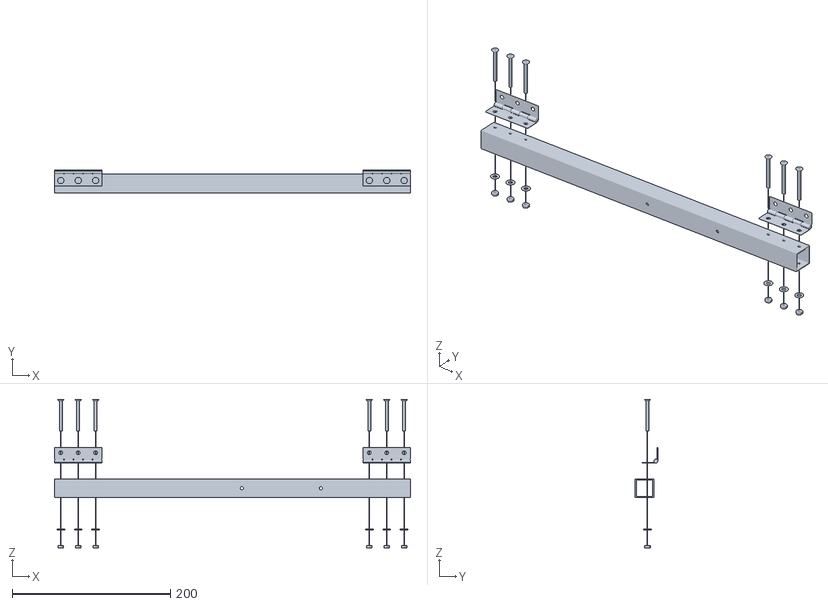
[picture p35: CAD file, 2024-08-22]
mechanics/web_viewer/models/panel_horizontal_axis_exploded.stl
450.0 x 28.5 x 188.3

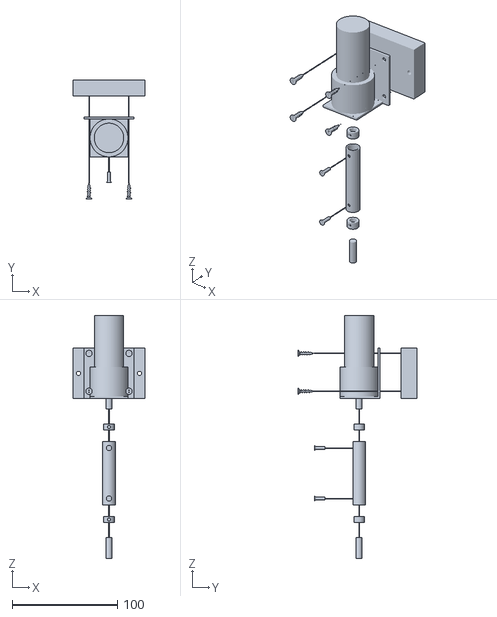
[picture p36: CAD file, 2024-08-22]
mechanics/web_viewer/models/motor_block_exploded.stl
68.0 x 113.0 x 231.0

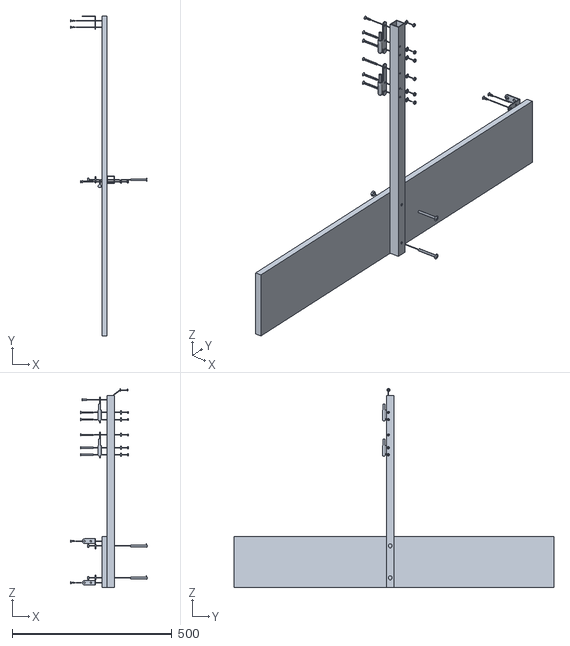
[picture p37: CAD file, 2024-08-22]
mechanics/web_viewer/models/stand_front_board_exploded.stl
239.2 x 1000.0 x 622.0

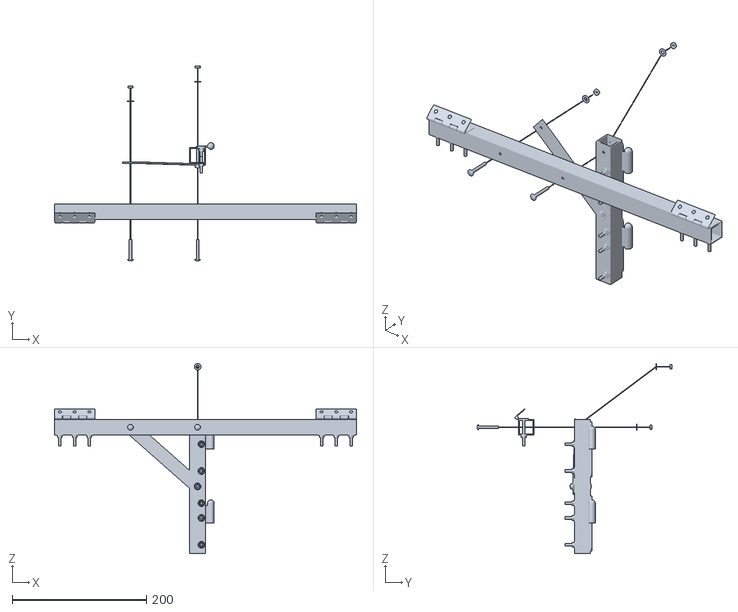
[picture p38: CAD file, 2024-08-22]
mechanics/web_viewer/models/panel_frame_exploded.stl
450.0 x 290.6 x 283.2

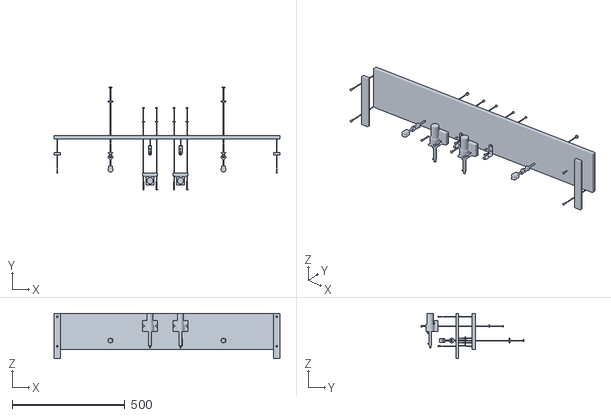
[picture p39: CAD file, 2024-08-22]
mechanics/web_viewer/models/stand_back_board_exploded.stl
1000.0 x 457.6 x 200.0

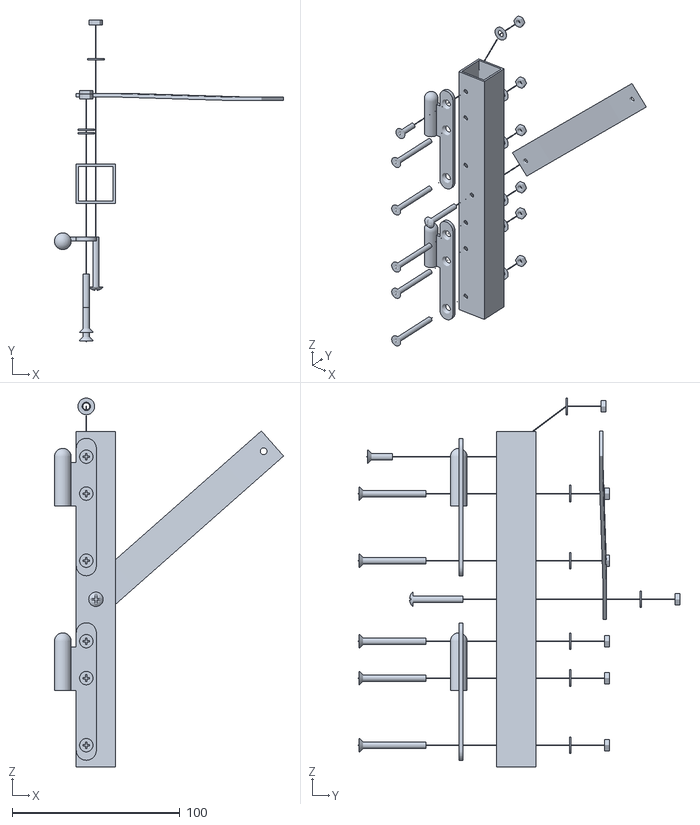
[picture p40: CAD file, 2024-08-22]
mechanics/web_viewer/models/panel_vertical_axis_exploded.stl
136.6 x 191.8 x 220.0

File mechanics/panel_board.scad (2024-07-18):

use <bolt_and_nut.scad>
use <assembly.scad>
use <big_bracket.scad>
use <pulley.scad> // Only for the "ring" part

$fa = 10;
$fs = 0.1;

GAP = 20;

EXPLODED = false;

skip_mirror_holders = false; // (for temporary manual speed up because 24 mirror holders make my computer slow)

mirror_width = 150;
mirror_depth = 4;
mirror_height = 150;

mirror_holder_width = 130;
mirror_holder_depth = 10;
mirror_holder_height = 130;
mirror_holder_pos_y = -20;
mirror_holder_middle_bolt_z = 15; // from mirror_holder center

mirror_holder_bolt_t = [ // from mirror_holder center
  [-55,0,55],
  [55,0,55],
  [0,0,-55]
];

mirror_columns = 4;
mirror_rows = 6;

mirror_period_x = mirror_width + 5;
mirror_period_z = mirror_height + 5;

panel_board_width = mirror_columns * mirror_period_x;
function panel_board_depth() = 15;
panel_board_bottom_margin = 30;
panel_board_height = mirror_rows * mirror_period_z;
panel_board_total_height = panel_board_height + panel_board_bottom_margin;

ring_hole_x = 20; // From bottom corners
ring_hole_z = 15; // From bottom corners

bracket_pos_z = -100; // From top border

glue_radius=3;
glue_corner_radius=20;
glue_linear_side_length=70;

module mirror_glue() {
  rotate([90,0,0])
    for (a=[0:90:270]) {
      rotate([0,0,a]) {
          translate([glue_linear_side_length/2, glue_linear_side_length/2, 0])
            rotate_extrude(angle=90)
                translate([glue_corner_radius, 0]) circle(glue_radius);

          translate([glue_linear_side_length/2+glue_corner_radius, glue_linear_side_length/2, 0])
            rotate([90, 0, 0])
                cylinder(r=glue_radius, h=glue_linear_side_length);
      }
    }
}

module mirror(exploded) {
  translate([0,-mirror_depth-(exploded?8*GAP:0),0]) {
    translate([-mirror_width/2,0,-mirror_height/2])
      cube([mirror_width,mirror_depth,mirror_height]);

    // Add fake mirror image lines
    translate([-mirror_width/4,0,-mirror_height/5])
      rotate([0,45,0])
        cylinder(mirror_width/1.5, r=0.5, $fn=4);
    translate([-mirror_width/3,0,mirror_height/8])
      rotate([0,45,0])
        cylinder(mirror_width/4, r=0.5, $fn=4);
    translate([mirror_width/3,0,-mirror_height/8])
      rotate([0,225,0])
        cylinder(mirror_width/4, r=0.5, $fn=4);
  }

  if(exploded) {
    for (a=[0:90:270]) {
      rotate([0,a,0]) {
        translate([mirror_holder_width/2,0,mirror_holder_height/2])
          rotate([90,0,0])
            cylinder(8*GAP, r=exploded_line_radius());
      }
    }
  }
}

module mirror_holder(exploded, angle_x, angle_z) {
  translate([0,mirror_holder_pos_y-mirror_holder_depth,mirror_holder_middle_bolt_z]) {
    rotate([90,0,0])
      bolt_assembly_m4(
        bolt_length=60,
        bolt_gap_z=6*GAP,
        assembly_depth=mirror_holder_depth-mirror_holder_pos_y+panel_board_depth(),
        washer_gap_z=3*GAP,
        exploded=exploded)
        countersunk_bolt_m4(60);

    translate([0,-(exploded?4*GAP:0),0]) {
      rotate([angle_x,0,angle_z]) {
        difference() {
          translate([-mirror_holder_width/2,0,-mirror_holder_height/2-mirror_holder_middle_bolt_z])
            cube([mirror_holder_width,mirror_holder_depth,mirror_holder_height]);

          translate([0,-1,0])
            rotate([-90,0,0]) {
              cylinder(mirror_holder_depth+2,r=2.5);
              cylinder(4,r1=6,r2=2.5);
            }
        }

        translate([0,0,-mirror_holder_middle_bolt_z]) {
          mirror_glue();
          translate([0,-glue_radius+1,0])
            mirror(exploded);
        }
      }
    }
  }
}

module panel_board(exploded=false) {
  difference() {
    translate([-panel_board_width/2,0,-panel_board_height/2-panel_board_bottom_margin])
      cube([panel_board_width,panel_board_depth(),panel_board_total_height]);

    for (c=[0:mirror_columns-1]) {
      x = mirror_period_x * (-(mirror_columns-1)/2 + c);
      for (r=[0:mirror_rows-1]) {
        z = mirror_period_z * (-(mirror_rows-1)/2 + r);
        translate([x,-1,z]) {
          translate([0,0,mirror_holder_middle_bolt_z])
            rotate([-90,0,0])
              cylinder(panel_board_depth()+2,r=2.5);
          for (hole_t=mirror_holder_bolt_t) {
            translate(hole_t)
              rotate([-90,0,0])
                cylinder(panel_board_depth()+2,r=3);
          }
        }
      }
    }

    for (x=[-panel_board_width/2+ring_hole_x,panel_board_width/2-ring_hole_x]) {
      translate([x,-1,-panel_board_height/2-panel_board_bottom_margin+ring_hole_z])
        rotate([-90,0,0])
          cylinder(panel_board_depth()+2,r=3);
    }
  }

  if(!skip_mirror_holders) {
    for (c=[0:mirror_columns-1]) {
      x = mirror_period_x * (-(mirror_columns-1)/2 + c);
      angle_z = -x/60; // not the exact angle, just to show some mirror orientation
      for (r=[0:mirror_rows-1]) {
        z = mirror_period_z * (-(mirror_rows-1)/2 + r);
        angle_x = z/60; // not the exact angle, just to show some mirror orientation

        if(!exploded || (c==0&&r==1)){
          translate([x,0,z]){
            mirror_holder(exploded, angle_x, angle_z);

            for (hole_t=mirror_holder_bolt_t) {
              translate(hole_t+[0,panel_board_depth()+20,0])
                rotate([-90,0,0])
                  impact_nut_assembly_m4(30, bolt_gap_z=5*GAP, assembly_depth=panel_board_depth()+20,exploded=exploded)
                    countersunk_bolt_m4(60);
            }
          }
        }
      }
    }
  }

  for (x=[-panel_board_width/2+ring_hole_x,panel_board_width/2-ring_hole_x]) {
    translate([x,panel_board_depth(),-panel_board_height/2-panel_board_bottom_margin+ring_hole_z])
      rotate([-90,0,0])
        bolt_assembly_m6(bolt_length=40,bolt_gap_z=3*GAP,assembly_depth=panel_board_depth(),washer_gap_z=GAP,nut_gap_z=2*GAP,exploded=exploded)
          rotate([-90,0,0])
            fixed_ring(30);
  }

  translate([0,panel_board_depth()+(exploded?9*GAP:0),panel_board_height/2+bracket_pos_z]){
    big_bracket();

    for (hole_t=big_bracket_origin_to_vertical_holes_t()) {
      translate(hole_t+[0,big_bracket_depth()+2,0])
        rotate([-90,0,0])
          simple_assembly(15,gap=3*GAP,extra_line_length=9*GAP,exploded=exploded)
            wood_screw_d4(15);
    }
  }
}

panel_board(EXPLODED);

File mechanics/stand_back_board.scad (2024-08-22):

use <bolt_and_nut.scad>
use <square_tube.scad>
use <assembly.scad>
use <small_bracket.scad>
use <motor_block.scad>
use <stand_front_board.scad>
use <pulley.scad>

$fa = 10;
$fs = 0.1;

function stand_vertical_axis_length() = 600;

function back_board_width() = 1000;
function back_board_depth() = 15;
function back_board_height() = front_board_height();

GAP = 30;

EXPLODED = true;

stand_pulley_offset_x = 250;
stand_pulley_offset_z = 40;

motor_block_offset_x = 60;
motor_block_offset_y = -motor_support_axis_offset();
motor_block_offset_z = 80;

bracket_offset_z = 15;

leg_width = 28;
leg_depth = 10;
leg_height = 200;
leg_hole_offset = 15;
leg_holes_t = [for (z = [leg_height-back_board_height()+leg_hole_offset,leg_height-leg_hole_offset]) [leg_width/2,-1,z] ];

module stand_back_board(exploded=false, gap=GAP) {
  difference() {
    translate([-front_board_length()/2,0,0])
      cube([back_board_width(),back_board_depth(),back_board_height()]);

    for (x=[-stand_pulley_offset_x,stand_pulley_offset_x]) {
      translate([x,-1,stand_pulley_offset_z])
        rotate([-90,0,0])
          cylinder(back_board_depth()+2,r=3);
    }

    for (x=[-motor_block_offset_x-back_board_depth(),motor_block_offset_x]) {
      translate([x,0,motor_block_offset_z]) {
        for (hole_t=motor_support_holes_t()) {
          translate([hole_t.x,-1,hole_t.z])
            rotate([-90,0,0])
              cylinder(back_board_depth()+2,r=2);
        }
      }
    }
  }

  for (x=[-stand_pulley_offset_x,stand_pulley_offset_x]) {
    translate([x,0,stand_pulley_offset_z])
      rotate([90,0,0])
        bolt_assembly_m6(bolt_length=40,assembly_depth=back_board_depth(),washer_gap_z=5*gap,nut_gap_z=2*gap,exploded=exploded)
          vertical_pulley(40);
  }

  for (x=[-motor_block_offset_x-back_board_depth(),motor_block_offset_x]) {
    translate([x,motor_block_offset_y-(exploded?5*gap:0),motor_block_offset_z]) {
      motor_block();

      for (hole_t=motor_support_holes_t()) {
        translate(hole_t)
          rotate([90,0,0])
            bolt_assembly_m4(bolt_length=40, assembly_depth=back_board_depth()+motor_support_depth(),washer_gap_z=7*gap,nut_gap_z=2*gap, exploded=exploded)
              round_head_bolt_m4(40);
      }
    }
    translate([x,exploded?-gap:0,bracket_offset_z]){
      small_bracket();
      for (hole_t=small_bracket_origin_to_vertical_holes_t()) {
        translate(hole_t + [0,-1,0])
          rotate([90,0,0])
            simple_assembly(15,exploded=exploded,extra_line_length=gap) {
              wood_screw_d4(15);
            }
      }
    }
  }

  for (x=[-back_board_width()/2,back_board_width()/2-leg_width]) {
    translate([x,-leg_depth-(exploded?2*gap:0),back_board_height() - leg_height]) {
      difference() {
        cube([leg_width,leg_depth,leg_height]);
        for (hole_t=leg_holes_t) {
          translate(hole_t)
            rotate([-90,0,0])
              cylinder(leg_depth+2,r=2);
        }
      }
      for (hole_t=leg_holes_t) {
        translate(hole_t)
          rotate([90,0,0])
            simple_assembly(20,exploded=exploded,extra_line_length=2*gap,gap=2*gap) {
              wood_screw_d4(20);
        }
      }
    }
  }
}

stand_back_board(EXPLODED, GAP);

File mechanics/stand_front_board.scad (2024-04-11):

use <bolt_and_nut.scad>
use <square_tube.scad>
use <left_hinge.scad>
use <panel_vertical_axis.scad>
use <assembly.scad>
use <small_bracket.scad>

$fa = 3;
$fs = 0.4;

function stand_vertical_axis_length() = 600;

function front_board_width() = 15;
function front_board_length() = 1000;
function front_board_height() = 160;

GAP = 20;

EXPLODED = true;


function stand_vertical_axis_origin_to_hinges_t() = [
  for (hinge_t = panel_vertical_axis_origin_to_hinges_t())
    hinge_t + [square_tube_width(),stand_vertical_axis_length()-panel_vertical_axis_length(),0]
];

stand_vertical_axis_hole_offset = 30;

function stand_board_bracket_offset() = 15;

function stand_vertical_axis_origin_to_stand_holes_t() = [
  [square_tube_width()/2,stand_vertical_axis_hole_offset,0],
  [square_tube_width()/2,front_board_height()-stand_vertical_axis_hole_offset,0]
];

// Work along y axis because it's the natural orientation of internal objects
module stand_vertical_axis_along_y(exploded, gap) {
  // square tube with all required holes
  difference() {
    square_tube(stand_vertical_axis_length());
    // Holes for left hinge
    for (hinge_t=stand_vertical_axis_origin_to_hinges_t()) {
      for (hole_t=hinge_male_origin_to_holes_t()) {
        t = hinge_t + hole_t;
        short_bolt = (t[1]>stand_vertical_axis_length()-20); // specific case for the last bolt : shorter because another bolt will be in the same axis
        translate(t + [0,0,1])
          rotate([180,0,0])
            cylinder(square_tube_width()+(short_bolt?-5:2),2,2);
      }
    }

    // Hole for stand assembly
    for (hole_t=stand_vertical_axis_origin_to_stand_holes_t()) {
      translate(hole_t + [0,0,-1])
        cylinder(square_tube_width()+2,3,3);
    }
  }

  for (hinge_t=stand_vertical_axis_origin_to_hinges_t()) {
    translate([0,0,exploded?gap:0])
      translate(hinge_t)
        left_hinge_male();

    for (hole_t=hinge_male_origin_to_holes_t()) {
      bolt_t = hinge_t+hole_t+[0,0,hinge_depth()];
      translate(bolt_t) {
        if(bolt_t[1]>stand_vertical_axis_length()-20) {
          // specific case for the last bolt : shorter because another bolt will be in the same axis
          bolt_assembly_m4(bolt_length=15, bolt_gap_z=3*GAP, assembly_depth=square_tube_depth()+hinge_depth(), washer_gap_y = 1.5*GAP, washer_gap_z = 2*GAP, exploded=exploded)
            countersunk_bolt_m4(15);
        }
        else {
          bolt_assembly_m4(bolt_length=40, bolt_gap_z=2*GAP, assembly_depth=square_tube_width()+hinge_depth(), exploded=exploded)
            countersunk_bolt_m4(40);
        }
      }
    }
  }

  // Bolts for stand assembly
  for (bolt_t=stand_vertical_axis_origin_to_stand_holes_t()) {
    translate(bolt_t)
      rotate([180,0,0])
        bolt_assembly_m6(bolt_length=60, bolt_gap_z=2*GAP, assembly_depth=square_tube_width()+front_board_width(), exploded=exploded)
          round_head_bolt_m6(50);
  }
}

module board(exploded, gap) {
  difference() {
    translate([-front_board_width(),-front_board_length()/2,0])
      cube([front_board_width(),front_board_length(),front_board_height()]);

    for (z=[stand_vertical_axis_hole_offset,front_board_height() - stand_vertical_axis_hole_offset]) {
      translate([-front_board_width()-1,-square_tube_width()/2,z])
        rotate([0,90,0])
          cylinder(front_board_width()+2,3,3);
    }
  }

  for (z=[stand_board_bracket_offset(),front_board_height() - stand_board_bracket_offset()]) {
    translate([-front_board_width()-(exploded?gap:0),front_board_length()/2,z]) {
      rotate([0,-90,0]) {
        small_bracket();

        for (hole_t=small_bracket_origin_to_horizontal_holes_t()) {
          translate(hole_t + [0,0,small_bracket_depth()+1])
            simple_assembly(15,exploded=exploded,gap=3*gap,extra_line_length=gap)
              wood_screw_d4(15);
        }
      }
    }
  }
}

module stand_front_board(exploded=false, gap=GAP) {
  translate([square_tube_width(),0,0])
    rotate([90,0,-90])
      stand_vertical_axis_along_y(exploded, gap);

  board(exploded, gap);
}

stand_front_board(EXPLODED, GAP);

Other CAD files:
mechanics/web_viewer/models/panel_board_exploded.stl
mechanics/motor.scad
mechanics/animated_solar_panel.scad
mechanics/assembly.scad
mechanics/big_bracket.scad
mechanics/bolt_and_nut.scad
mechanics/flat_profile.scad
mechanics/left_hinge.scad
mechanics/motor_block.scad
mechanics/panel_frame.scad
mechanics/panel_horizontal_axis.scad
mechanics/panel_vertical_axis.scad
mechanics/pulley.scad
mechanics/small_bracket.scad
mechanics/small_hinge.scad
mechanics/solar_panel.scad
mechanics/square_tube.scad
mechanics/stand.scad

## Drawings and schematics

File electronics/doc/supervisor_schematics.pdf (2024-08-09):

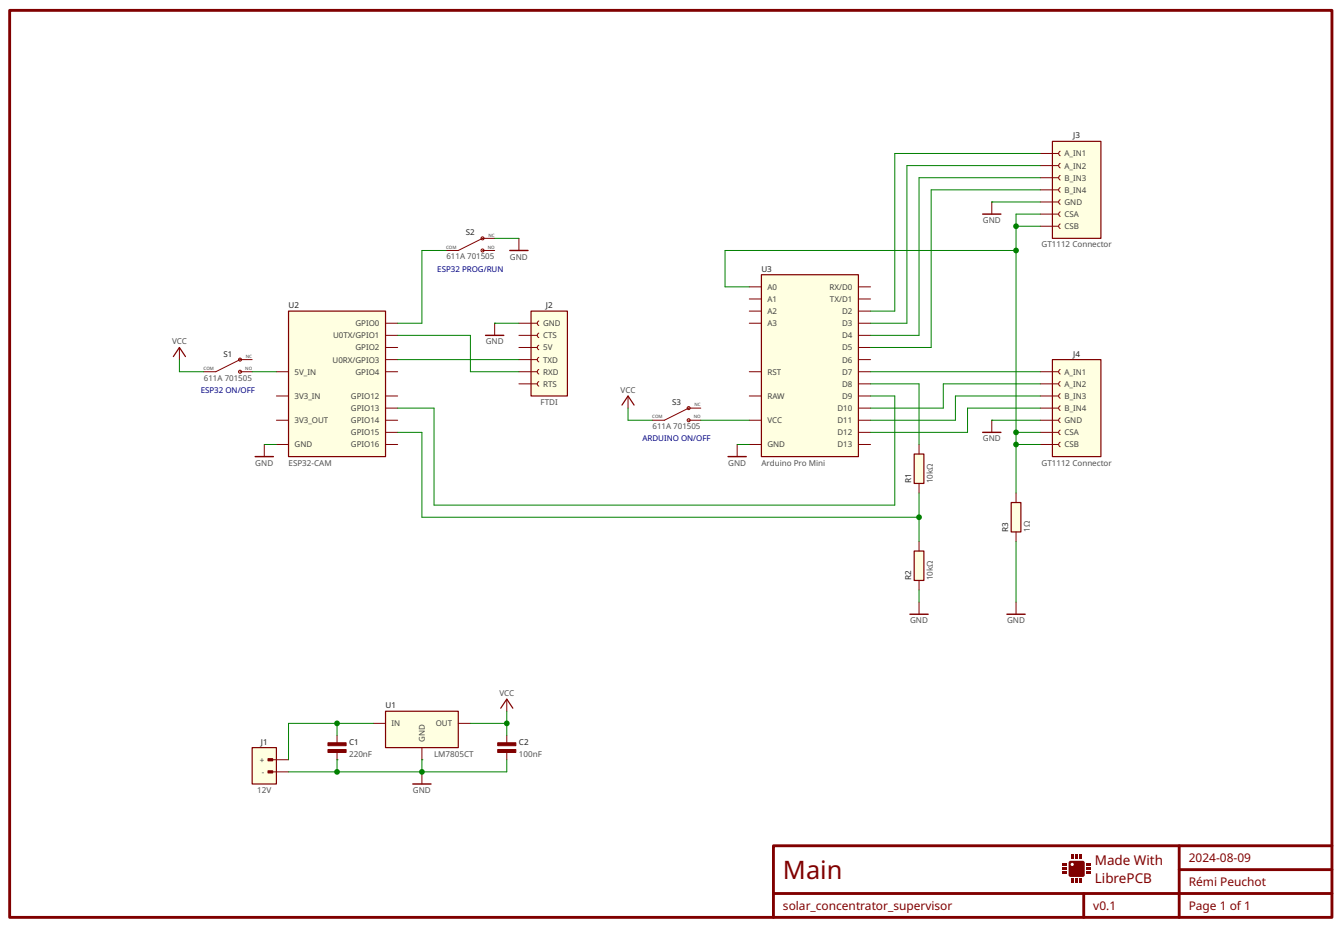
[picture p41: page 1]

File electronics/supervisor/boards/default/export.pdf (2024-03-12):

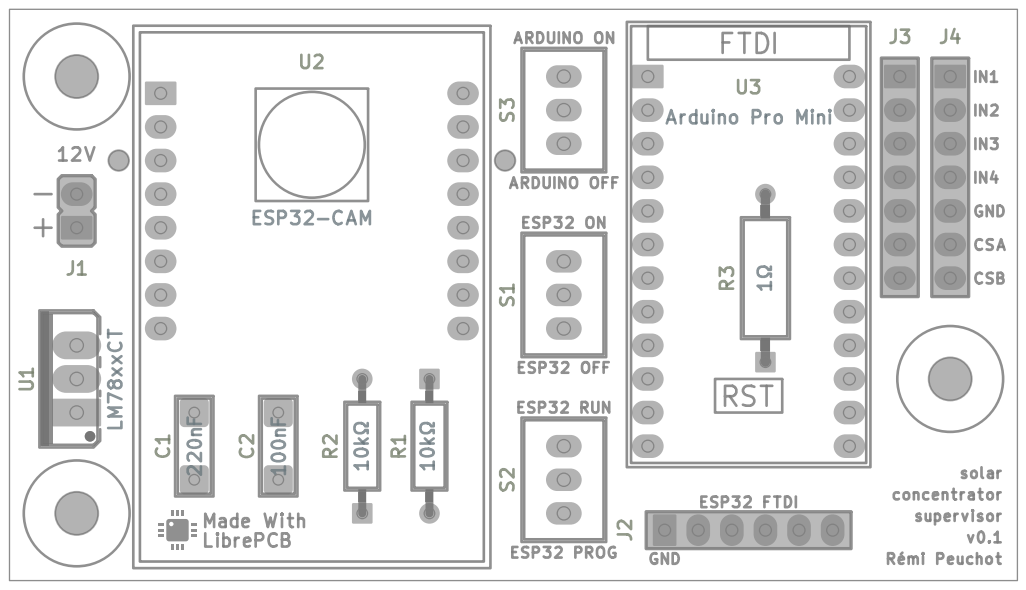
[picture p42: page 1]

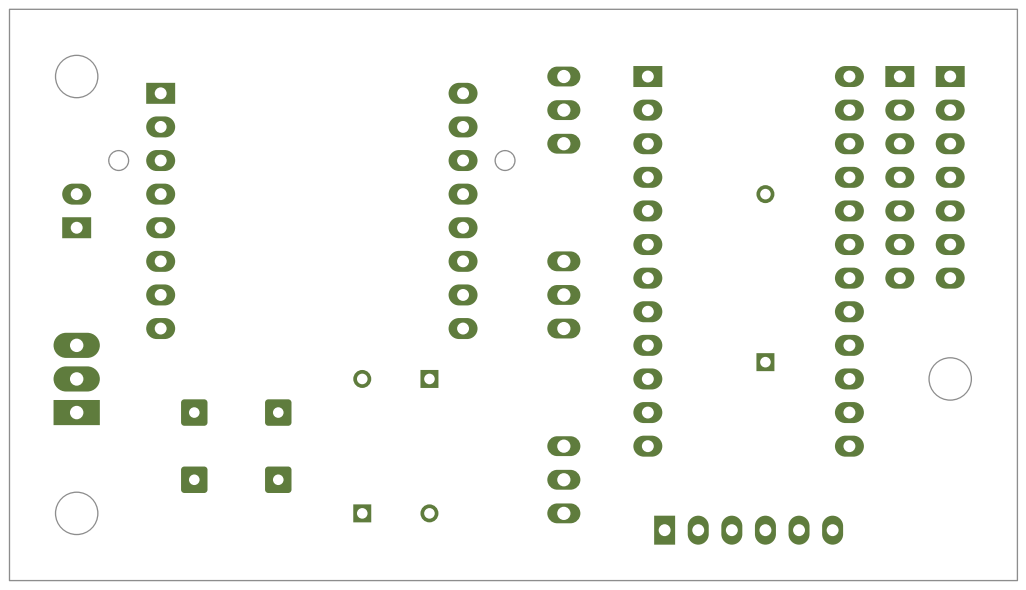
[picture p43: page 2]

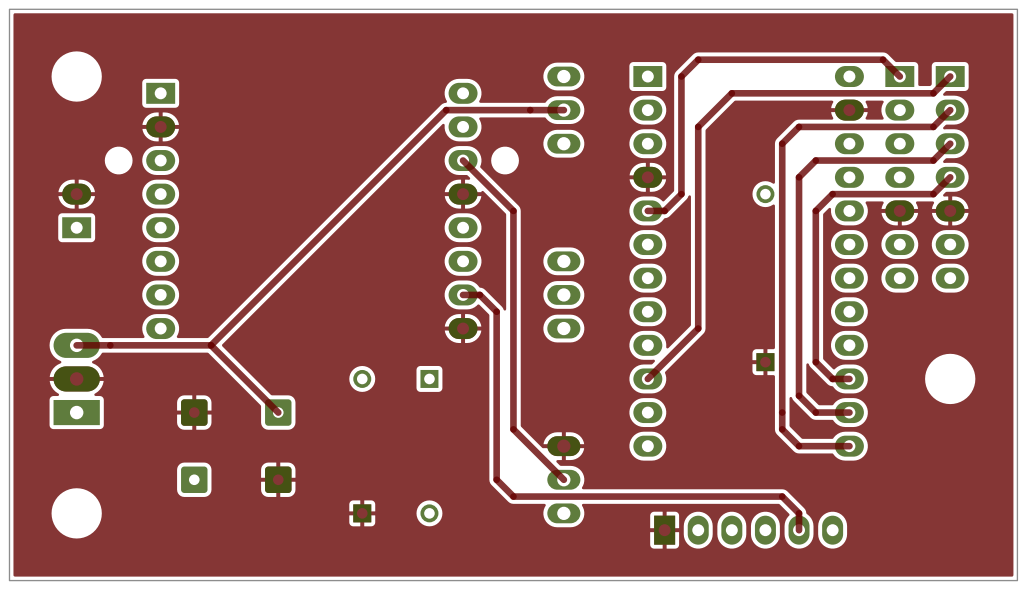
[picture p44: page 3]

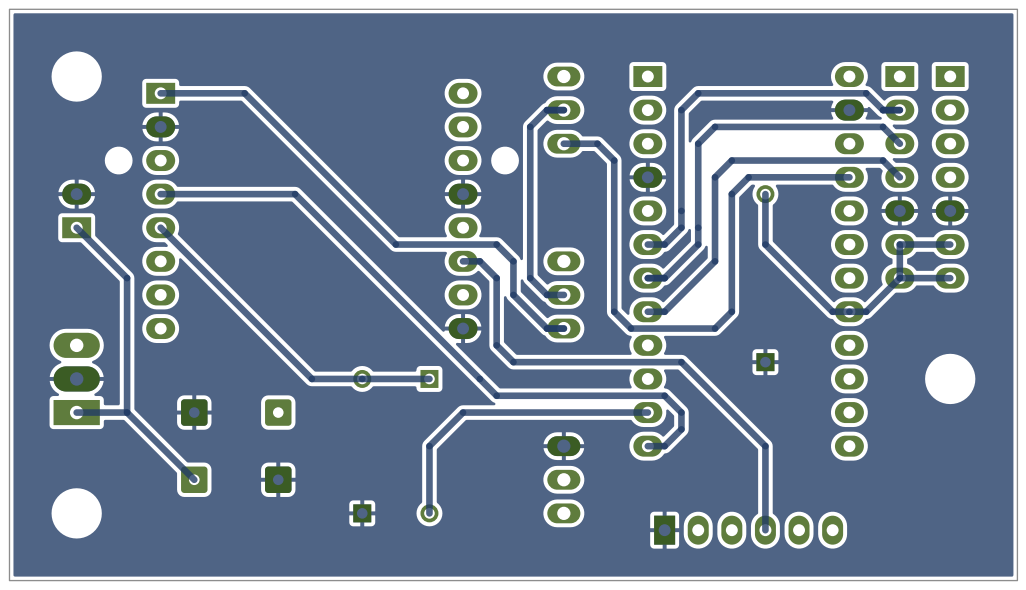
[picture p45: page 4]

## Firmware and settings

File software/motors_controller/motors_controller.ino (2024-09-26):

// Copyright (C) 2024 Rémi Peuchot (https://remipch.github.io/)
// This code is distributed under GNU GPL v3 license

#include <SoftwareSerial.h>

const int MOTOR_PINS_COUNT = 8;

// Motor pins ordered by motors command bit (loweest bit at index 0)
int MOTOR_PINS[MOTOR_PINS_COUNT] = {
    // PANEL_0:
    2, //  LEFT motor, pin A (unroll)   1
    3, //  LEFT motor, pin B (roll)     2
    4, //  RIGHT motor, pin A (unroll)  4
    5, //  RIGHT motor, pin B (roll)    8
    // PANEL_1:
    7, // LEFT motor, pin A (unroll)   16
    10, // LEFT motor, pin B (roll)     32
    11, // RIGHT motor, pin A (unroll)  64
    12, // RIGHT motor, pin B (roll)    128
};

int PWM_PIN = 6; // dedicated to motors speed

int MEASURE_PIN = A0;

// Soft serial pins (connection with ESP32 master)
int SOFT_RX_PIN = 9;
int SOFT_TX_PIN = 8;

SoftwareSerial MasterSerial(SOFT_RX_PIN, SOFT_TX_PIN);

void setup()
{
    MasterSerial.begin(19200);
    Serial.begin(19200);

    pinMode(LED_BUILTIN, OUTPUT);
    for (int i = 0; i < MOTOR_PINS_COUNT; i++) {
        pinMode(MOTOR_PINS[i], OUTPUT);
    }
    pinMode(PWM_PIN, OUTPUT);
    analogWrite(PWM_PIN, 255);

    printRam();
    printSampling();
    stopAndClearCommands();
}

void loop()
{
    String commands = "";
    if (Serial.available() > 0) {
        commands = Serial.readStringUntil('\n');
    } else if (MasterSerial.available() > 0) {
        commands = MasterSerial.readStringUntil('\n');
    }
    if (commands.length() > 0) {
        Serial.print("parse commands: ");
        Serial.println(commands);
        parseAndRunCommands(commands);
    }

    // Start/update/terminate commands depending on command buffer and current command state
    run();
}

void printRam()
{
    extern unsigned int __data_start;
    extern unsigned int __bss_start;
    extern unsigned int __heap_start;
    extern void* __brkval;
    byte stack_start;
    unsigned int heap_end = (__brkval == 0 ? (unsigned int)&__heap_start : (unsigned int)__brkval);
    unsigned int stackSize = RAMEND - (unsigned int)&stack_start + 1;
    unsigned int freeMem = ((unsigned int)&stack_start) - heap_end;

    Serial.print(F("data : "));
    Serial.print((unsigned int)&__bss_start - (unsigned int)&__data_start);
    Serial.print(F(" byte(s) from 0x"));
    Serial.println((unsigned int)&__data_start, 16);

    Serial.print(F("bss : "));
    Serial.print((unsigned int)&__heap_start - (unsigned int)&__bss_start);
    Serial.print(F(" byte(s) from 0x"));
    Serial.println((unsigned int)&__bss_start, 16);

    Serial.print(F("heap : "));
    Serial.print(heap_end - (unsigned int)&__heap_start);
    Serial.print(F(" byte(s) from 0x"));
    Serial.println((unsigned int)&__heap_start, 16);

    Serial.print(F("stack : "));
    Serial.print(stackSize);
    Serial.print(F(" byte(s) from 0x"));
    Serial.println((unsigned int)&stack_start, 16);

    Serial.print(F("free RAM : "));
    Serial.print(freeMem);
    Serial.println(F(" bytes"));
    Serial.println();
}

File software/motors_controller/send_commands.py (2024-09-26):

# Copyright (C) 2024 Rémi Peuchot (https://remipch.github.io/)
# This code is distributed under GNU GPL v3 license

import getch

import serial

motors = serial.Serial('/dev/ttyUSB0',baudrate=19200)

def writeCommand(info, command):
    print(info,flush=True)
    res = motors.write((command + "\n").encode())
    print(str(res) + " byte(s) written")

def readResult():
    res = motors.read(1000).decode("utf-8")
    print(res)

# read the initial text with bigger timeout
motors.timeout = 2
readResult()
motors.timeout = 0.5

print("Waiting for direction digit keys",flush=True)

while True:
    ch = getch.getch()
    if ord(ch)==27: # escape
        exit()
    elif ch == 's':
        writeCommand("Status", "s")
    elif ch == 'm':
        writeCommand("Measure buffer", "m:100")
    elif ch == 'a':
        writeCommand("Unroll all", "o:21,1000,80")
    elif ch == 'A':
        writeCommand("Roll all", "o:42,1000,80")
    elif ch == 'u':
        writeCommand("Unroll up", "o:1,1000,30")
    elif ch == 'U':
        writeCommand("Roll up", "o:2,5000,30")
    elif ch == 'j':
        writeCommand("Unroll down right", "o:4,1000,30")
    elif ch == 'J':
        writeCommand("Roll down right", "o:8,5000,30")
    elif ch == 'h':
        writeCommand("Unroll down left", "o:16,1000,30")
    elif ch == 'H':
        writeCommand("Roll down left", "o:32,5000,30")
    elif ch == '0':
        writeCommand("Off", "o:0,1000")
    elif ch == '8':
        writeCommand("Step UP", "o:20,200,100;o:2,5000,30;o:42,1000,80")
    elif ch == '9':
        writeCommand("Step UP_RIGHT", "o:16,200,100;o:2,5000,30;o:42,1000,80")
    elif ch == '6':
        writeCommand("Step RIGHT", "o:16,200,100;o:8,5000,30;o:42,1000,80")
    elif ch == '3':
        writeCommand("Step DOWN_RIGHT", "o:1,200,100;o:8,5000,30;o:42,1000,80")
    elif ch == '2':
        writeCommand("Step DOWN", "o:1,200,100;o:40,5000,30;o:42,1000,80")
    elif ch == '1':
        writeCommand("Step DOWN_LEFT", "o:1,200,100;o:32,5000,30;o:42,1000,80")
    elif ch == '4':
        writeCommand("Step LEFT", "o:4,200,100;o:32,5000,30;o:42,1000,80")
    elif ch == '7':
        writeCommand("Step UP_LEFT", "o:4,200,100;o:2,5000,30;o:42,1000,80")
    else:
        print("unkown key")
        continue
    readResult()

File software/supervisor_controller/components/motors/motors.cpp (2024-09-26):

// Copyright (C) 2024 Rémi Peuchot (https://remipch.github.io/)
// This code is distributed under GNU GPL v3 license

#include "motors.hpp"
#include "motors_state_machine.hpp"

#include "esp_log.h"

#include "freertos/FreeRTOS.h"
#include "freertos/semphr.h"
#include <vector>

static const char *TAG = "motors";

// This file is the public interface of the motors component
// It does not implement logic by itself but provides thread safety to state_machine layer
// It's accomplished by :
// - preventing multiple simultaneous calls to state_machine functions
//   by calling them from a dedicated task
// - protecting state and transition values with a mutex
static const int STATE_MUTEX_TIMEOUT_MS = 100;
static SemaphoreHandle_t state_mutex;
static const int INTER_UPDATE_DELAY_MS = 100;
static motors_state_t current_state = motors_state_t::UNINITIALIZED;
static motors_transition_t asked_transition = motors_transition_t::NONE;
static motors_direction_t asked_direction = motors_direction_t::NONE;
static std::vector<motors_stopped_callback> stopped_callbacks;

void motors_register_stopped_callback(motors_stopped_callback callback) { stopped_callbacks.push_back(callback); }

// This function must not be called from an ISR (interrupt service routine)
// because mutex does not support it. Neither ESP32 doc nor FreeRTOS doc is clear
// about what happens in this case, various forums seem to indicate that an 'abort()'
// is triggered with an explanation message.
const char *motors_get_state()
{
    assert(xSemaphoreTake(state_mutex, pdMS_TO_TICKS(STATE_MUTEX_TIMEOUT_MS)));
    auto state = current_state;
    xSemaphoreGive(state_mutex);
    return str(state);
}

// Note : transition will be reset if state changes after this call
void set_transition(motors_transition_t transition, motors_direction_t direction = motors_direction_t::NONE)
{
    assert(xSemaphoreTake(state_mutex, pdMS_TO_TICKS(STATE_MUTEX_TIMEOUT_MS)));
    if (asked_transition != motors_transition_t::NONE) {
        ESP_LOGW(
            TAG,
            "Old transition '%s' ignored because new transition '%s' is asked before the old transition processing",
            str(asked_transition),
            str(transition));
    }
    asked_transition = transition;
    asked_direction = direction;
    xSemaphoreGive(state_mutex);
}

static void motors_task(void *arg)
{
    while (true) {
        assert(xSemaphoreTake(state_mutex, pdMS_TO_TICKS(STATE_MUTEX_TIMEOUT_MS)));
        motors_state_t state = current_state;
        motors_transition_t transition = asked_transition;
        motors_direction_t direction = asked_direction;

        // Reset asked transition :
        // - it will be "consumed" by 'state_machine_update' outside of the mutex guard
        // - one transition must not be treated multiple times by 'state_machine_update'
        // - we allow another transition to be set while 'state_machine_update' is running
        asked_transition = motors_transition_t::NONE;
        asked_direction = motors_direction_t::NONE;
        xSemaphoreGive(state_mutex);

        motors_state_t new_state = motors_state_machine_update(state, transition, direction);

        if (new_state != state) {
            ESP_LOGI(TAG,
                     "update(state: %s, transition: %s, direction: %s) -> new_state: %s",
                     str(state),
                     str(transition),
                     str(direction),
                     str(new_state));
        }

        assert(xSemaphoreTake(state_mutex, pdMS_TO_TICKS(STATE_MUTEX_TIMEOUT_MS)));
        if (current_state != motors_state_t::STOPPED && new_state == motors_state_t::STOPPED) {
            for (auto callback : stopped_callbacks) {
                callback();
            }
        }
        current_state = new_state;
        xSemaphoreGive(state_mutex);

        // Simple wait between state updates because :
        // - don't need a strict period between state updates (don't use periodic timer)
        // - don't need to treat event as fast as possible
        vTaskDelay(pdMS_TO_TICKS(INTER_UPDATE_DELAY_MS));
    }
}

void motors_init()
{
    ESP_LOGD(TAG, "motors_init");

    assert(current_state == motors_state_t::UNINITIALIZED);

    state_mutex = xSemaphoreCreateMutex();

    xTaskCreate(motors_task, TAG, 4 * 1024, NULL, 5, NULL);
}

void motors_start_move_continuous(motors_direction_t direction)
{
    set_transition(motors_transition_t::START_MOVE_CONTINUOUS, direction);
}

void motors_start_move_one_step(motors_direction_t direction)
{
    set_transition(motors_transition_t::START_MOVE_ONE_STEP, direction);
}

void motors_stop() { set_transition(motors_transition_t::STOP); }

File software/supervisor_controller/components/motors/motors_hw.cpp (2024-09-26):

// Copyright (C) 2024 Rémi Peuchot (https://remipch.github.io/)
// This code is distributed under GNU GPL v3 license

#include "motors_hw.hpp"

#include "driver/uart.h"
#include "esp_log.h"
#include "string.h"
static const char *TAG = "motors_hw";

#define MOTOR_CONTROLLER_RX_PIN 15
#define MOTOR_CONTROLLER_TX_PIN 13
#define MOTOR_CONTROLLER_UART_PORT_NUM 2
#define MOTOR_CONTROLLER_BAUD_RATE 19200

#define BUFFER_SIZE (128) // (keep small to stay below task stack size)

static const int REPLY_READ_TIME_MS = 80;

const char END_CHAR = '\n';

motor_hw_error_t motors_hw_init()
{
    esp_log_level_set(TAG, ESP_LOG_DEBUG);
    ESP_LOGI(TAG, "motors_hw_init");

    uart_config_t uart_config = {
        .baud_rate = MOTOR_CONTROLLER_BAUD_RATE,
        .data_bits = UART_DATA_8_BITS,
        .parity = UART_PARITY_DISABLE,
        .stop_bits = UART_STOP_BITS_1,
        .flow_ctrl = UART_HW_FLOWCTRL_DISABLE,
        .rx_flow_ctrl_thresh = 0,
        .source_clk = UART_SCLK_APB,
    };

    if (uart_driver_install(MOTOR_CONTROLLER_UART_PORT_NUM, BUFFER_SIZE * 2, 0, 0, NULL, 0) != ESP_OK)
        return motor_hw_error_t::CANNOT_USE_UART;
    if (uart_param_config(MOTOR_CONTROLLER_UART_PORT_NUM, &uart_config) != ESP_OK)
        return motor_hw_error_t::CANNOT_USE_UART;
    if (uart_set_pin(MOTOR_CONTROLLER_UART_PORT_NUM,
                     MOTOR_CONTROLLER_TX_PIN,
                     MOTOR_CONTROLLER_RX_PIN,
                     UART_PIN_NO_CHANGE,
                     UART_PIN_NO_CHANGE)
        != ESP_OK)
        return motor_hw_error_t::CANNOT_USE_UART;

    return motor_hw_error_t::NO_ERROR;
}

bool motors_hw_write_commands(const char *commands)
{
    ESP_LOGV(TAG, "Send '%s' to motors", commands);
    int res = uart_write_bytes(MOTOR_CONTROLLER_UART_PORT_NUM, commands, strlen(commands));
    res += uart_write_bytes(MOTOR_CONTROLLER_UART_PORT_NUM, &END_CHAR, 1);
    return (res == strlen(commands) + 1);
}

// Return true if the last character received is '1'
char motors_hw_read_reply()
{
    char reply[BUFFER_SIZE];
    int len =
        uart_read_bytes(MOTOR_CONTROLLER_UART_PORT_NUM, reply, (BUFFER_SIZE - 1), pdMS_TO_TICKS(REPLY_READ_TIME_MS));
    if (len > 0) {
        reply[len] = '\0';
        char result = reply[len - 1];
        ESP_LOGV(TAG, "Reply: '%s' (len: %i, result:'%c')", reply, len, result);
        return result;
    } else {
        ESP_LOGW(TAG, "No reply");
        return '?';
    }
}

void motors_hw_stop()
{
    ESP_LOGV(TAG, "motors_hw_stop");
    motors_hw_write_commands("c");
}

void motors_hw_start_move(motors_direction_t direction, bool continuous)
{
    ESP_LOGV(TAG, "motors_hw_start_move(direction = %s, continuous = %i)", str(direction), continuous ? 1 : 0);
    int motor_pins = 0;

    if (direction == motors_direction_t::UP) {
        motor_pins = 5;
    } else if (direction == motors_direction_t::UP_RIGHT) {
        motor_pins = 1;
    } else if (direction == motors_direction_t::RIGHT) {
        motor_pins = 9;
    } else if (direction == motors_direction_t::DOWN_RIGHT) {
        motor_pins = 8;
    } else if (direction == motors_direction_t::DOWN) {
        motor_pins = 10;
    } else if (direction == motors_direction_t::DOWN_LEFT) {
        motor_pins = 2;
    } else if (direction == motors_direction_t::LEFT) {
        motor_pins = 6;
    } else if (direction == motors_direction_t::UP_LEFT) {
        motor_pins = 4;
    } else {
        assert(false);
    }

    // Electronics support 2 panels (A and B) because it was planned to control 2 panels
    // but the current supervisor software manage only one panel.
    // The same command is sent to both panel outputs
    // so it works whatever the actual output connected to the real panel is
    motor_pins = motor_pins + (motor_pins * 16);

    // 'continuous' is not supposed to be infinite because hard angle limit
    int cmd_max_time_ms = continuous ? 10000 : 150;
    int cmd_threshold = 200;
    static char command[1024];
    sprintf(command, "o:%i,%i,%i", motor_pins, cmd_max_time_ms, cmd_threshold);
    motors_hw_write_commands(command);
}

motor_hw_state_t motor_hw_get_state()
{
    motors_hw_write_commands("s");

    char reply = motors_hw_read_reply();
    motor_hw_state_t state;
    if (reply == '1')
        state = motor_hw_state_t::MOVING;
    else if (reply == '0')
        state = motor_hw_state_t::STOPPED;
    else
        state = motor_hw_state_t::UNKNOWN;
    ESP_LOGV(TAG, "motor_hw_get_state(): %s", str(state));
    return state;
}

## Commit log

2023-04-19 initial commit (from restructured sun_follower_panel project)
    [partitions.csv]
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2023-04-25 panel_controller/motors: replace current measure by tensing phase duration
    (while there is no measure of current)
2023-04-25 Revert "panel_controller/motors: replace current measure by tensing phase duration"
    This reverts commit 42f6fe057e510aaa612b5fb600d54273c3c2b1fc.
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2023-05-25 motors_controller: does not work
    [motors_controller.ino]
2023-05-25 esp32 play with uart
    because I2C does not work :
    - level shift 5V <-> 3.3V
    - pullup not disablable
    - bidirectional
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2023-05-26 motors_controller: fix reply
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2023-05-26 [FIX_CRASH] motor_hw : reduce stack size
    [motors_hw.cpp]
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2023-05-28 motors_controller: install getch correctly
2023-05-28 fix esp32 hostname resolution from container
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2023-05-30 panel_controller: static IP address instead of mdns
    because mdns is buggy (loose network connection randomly)
    [app_httpd.cpp]
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2023-06-07 panel_web_access: wait a little bit in case of networking problems
2023-06-07 fixup! panel_web_access: wait a little bit in case of networking problems
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2023-09-30 restructure according to new architecture
    [partitions.csv]
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2023-10-11 camera: fix obsolete constants
2023-10-11 web: fix log tag
    [app_httpd.cpp]
2023-10-11 web: detect and treat camera errors
    [app_httpd.cpp]
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2023-10-11 web: purge old connection
    to avoid error "httpd_server: error accepting new connection"
    [app_httpd.cpp]
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2023-10-12 rename root supervisor directory to software
    [partitions.csv]
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2023-10-13 motors: increase reply timeout
    (quite less missing replies after that)
    [motors_hw.cpp]
2023-10-13 motors: little fixes
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2023-10-18 motors: detect hw errors
    [motors_state_machine.cpp, motors_state_machine_test.cpp]
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2023-11-21 enable clangd for esp32 build
    (see
    https://github.com/espressif/esp-idf/issues/6868#issuecomment-1075743763)
2023-11-23 docker : fix clangd for esp32 build
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2024-01-24 sun_tracker: fix bitfield enum
    [sun_tracker.cpp]
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2024-01-29 motors: remove up motor
    (didn't successfully managed cable tensing -> remove and replace by a
    simple mass)
    [motors_hw.cpp, send_commands_2.py]
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2024-01-29 supervisor: allow to reset in case of error
    [supervisor_state_machine.cpp]
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2024-01-30 web: replace stream button by checkbox
    m
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2024-01-31 sun_tracker: remove ERROR and SUCCESS states, they are results
    [sun_tracker.cpp, sun_tracker_state_machine.cpp, supervisor.cpp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]
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2024-02-07 target_detector: log capstones in case of wrong number of detected capstones
2024-02-07 supervisor: restart tracking a few times in case of sun_tracker error
    [supervisor_state_machine.cpp]
2024-02-07 sun_tracker: reset move_count on success, increment for each move
    because sun_tracker can be restarted in case of error, but we want to
    count the exact move_count (counting the starting move and the following
    moves)
    [sun_tracker_state_machine.cpp]
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2024-03-12 elec: fix missing wire
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2024-03-28 mecha: add left_hinge model
    [left_hinge.scad]
2024-03-29 mecha: add bolt and nut models
    [bolt_and_nut.scad]
2024-03-29 mecha: bolt_and_nut export usefull dimensions
    [bolt_and_nut.scad]
2024-03-29 mecha: bolt_and_nut shows assembly
    [bolt_and_nut.scad]
2024-03-29 mecha: left_hinge export usefull dimensions
    [left_hinge.scad]
2024-03-29 mecha: add square_tube model
    [square_tube.scad]
2024-03-29 mecha: colorize bolt and nuts
    to make them look appart in final design
    [bolt_and_nut.scad]
2024-03-29 mecha: add cross screw to countersunk bolt
    [bolt_and_nut.scad]
2024-03-29 mecha: left hinge hole offset from left limit of the platform
    [left_hinge.scad]
2024-03-29 mecha: export hinge depth
    [left_hinge.scad]
2024-03-29 mecha: add temp model to play with existing models
    [temp.scad]
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2024-04-07 mecha: adjust bolt diameter
    [bolt_and_nut.scad]
2024-04-07 mecha: add "exploded" param for temp
    [temp.scad]
2024-04-07 mecha: left_hinge more convenient center
    [left_hinge.scad]
2024-04-07 mecha: temp use left_hinge new center
    [temp.scad]
2024-04-07 mecha: explode hinge too
    [temp.scad]
2024-04-07 mecha: rename temp to panel_vertical _axis
    [panel_vertical_axis.scad]
2024-04-07 mecha: add small hinge
    [small_hinge.scad]
2024-04-07 mecha: left_hinge correct hole positions
    [left_hinge.scad]
2024-04-07 mecha: add cross to round head bolt
    [bolt_and_nut.scad]
2024-04-07 mecha: add bolt to support diagonal bar
    [panel_vertical_axis.scad]
2024-04-07 mecha: parametrize "explostion line" radius
    [panel_vertical_axis.scad]
2024-04-07 mecha: specific case for last bolt of vertical panel axis
    (it's shorter because another bolt will be in the same axis)
    [panel_vertical_axis.scad]
2024-04-07 mecha: add panel_horozontal axis
    [panel_horizontal_axis.scad]
2024-04-07 mecha: small hinge export its height
    [small_hinge.scad]
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2024-04-07 mecha: vertical axis offset hidden nut when exploded
    [panel_vertical_axis.scad]
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2024-04-07 mecha: add horizontal axis round head bolts
    to assemble diagonal bar and vertical axis
    [panel_horizontal_axis.scad]
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2024-04-07 mecha: horizontal axis round head bolts take depth into account
    [panel_horizontal_axis.scad]
2024-04-07 mecha: fix horizontal axis module name
    [panel_horizontal_axis.scad]
2024-04-07 mecha: fix round head bolt on vertical axis
    [panel_vertical_axis.scad]
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2024-04-07 mecha: vertical axis add hole for horizontal axis
    [panel_vertical_axis.scad]
2024-04-07 mecha: horizontal axis export length and accept exploded param
    [panel_horizontal_axis.scad]
2024-04-07 mecha: horizontal axis offset hidden nut when exploded
    [panel_horizontal_axis.scad]
2024-04-08 mecha: add flat profile for diagonal bar between vertical and horizontal axes
    [flat_profile.scad]
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2024-04-08 mecha: horizontal axis export "diagonal_fixpoint_offset_from_center_of_vertical_bar"
    and fix hole position
    [panel_horizontal_axis.scad]
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2024-04-08 mecha: horizontal axis parameter for round_head_bolt_assembly washer gap
    [panel_horizontal_axis.scad]
2024-04-08 mecha: fix exploded line lengths for bolts
    [panel_vertical_axis.scad]
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2024-04-09 mecha: add motor block screw and gap assemblies
    [motor_block.scad]
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2024-04-10 mecha: simple assembly line starts from screw end
    [assembly.scad, motor_block.scad]
2024-04-10 mecha: fix motor axis cylinder and locking ring
    [motor.scad, motor_block.scad]
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2024-04-10 mecha: panel_frame move bolt from horizontal axis to panel frame
    [panel_frame.scad, panel_horizontal_axis.scad, panel_vertical_axis.scad]
2024-04-10 mecha: stand vertical axis use generix bolt assembly M4
    [stand_vertical_axis.scad]
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2024-04-10 mecha: stand vertical axis use generix assembly M6
    [stand_vertical_axis.scad]
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2024-04-11 mecha: add motor block to stand back board
    [motor_block.scad, stand_back_board.scad]
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2024-04-11 mecha: adjust number of facets
    allowing :
    - smaller output stl files
    - while ensuring cylinder and sphere to be beautifully rendered in
    Online 3D Viewer with Edge Angle Treshold = 12° (remove lines between
    "almost coplanar" triangles)
    [bolt_and_nut.scad, left_hinge.scad, motor.scad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]
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2024-04-11 mecha: small bracket exports vertical and horizontal hole positions
    [motor_block.scad, small_bracket.scad, stand_front_board.scad]
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2024-04-11 mecha: ajust gaps in stand back board
    so everything is visible from a given view point
    [stand_back_board.scad]
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2024-04-11 mecha: ajust screw length in stand back board
    [stand_back_board.scad]
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2024-05-12 mecha: fix screw rotation direction
    [bolt_and_nut.scad]
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2024-06-06 sun_tracker: increase spot overrun
    (otherwise spot overrun can be wrongly detected if spot light is
    spreading due to sun light variation)
    [sun_tracker_logic.cpp]
2024-06-06 sun_tracker: set fixed light pixel level
    (old code is kept to simulate spot light inside with a white paper)
    [sun_tracker_logic.cpp]
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2024-07-10 Revert "mecha: add stand diagonal bar"
    This reverts commit 4472a36171822730a1519c46cde3ae30662e26c5.
    [stand.scad]
2024-07-10 mecha: assemble motor bloc with bolts instead of wood screws
    [stand_back_board.scad]
2024-07-11 mecha: add motor bloc holes in stand back board
    [stand_back_board.scad]
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2024-07-12 mecha: panel_board add mirror_holder
    and remove old copy pasted stuff
    [panel_board.scad]
2024-07-12 mecha: panel_board use correct gap when exploded
    [panel_board.scad]
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2024-07-12 mecha: panel_board add fixed rings
    [panel_board.scad]
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2024-07-18 mecha: correct orientation of small_hinge children
    [small_hinge.scad]
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2024-07-18 mecha: panel_frame fix 'gap' and 'exploded' parameter
    [panel_frame.scad]
2024-07-18 mecha: rotate and center panel_frame at vertical hinge axis
    [panel_frame.scad]
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2024-07-18 mecha: small_hinge add 'move_to_other_half' helper
    (will be used for other half screws)
    [small_hinge.scad]
2024-07-18 mecha: panel_horizontal_axis accept children to assemble panel board
    [panel_horizontal_axis.scad]
2024-07-18 mecha: panel add manual option to skip mirror holders
    [panel_board.scad]
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2024-08-22 mecha: fix stand gap
    [stand.scad]
2024-08-22 mecha: fix stand_back_board holes and gap
    [stand_back_board.scad]
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2024-08-26 mecha: move models to 'web_viewer/models' subfolder
    because they're exported to be used by the web_viewer
    [motor_block_assembled.stl, motor_block_exploded.stl, panel_board_exploded.stl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]
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2024-08-27 simu: invert left and right mouse button navigation role
    to match the 3D web_viewer commands
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
